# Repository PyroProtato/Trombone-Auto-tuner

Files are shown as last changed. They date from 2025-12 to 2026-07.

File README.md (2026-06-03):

# Trombone Autotuner



Hello! This is my first big personal hardware project. It's a custom autotuner for the Trombone! It should be able to detect whether the user is flat or sharp when playing a note and adjust the tuning slide to fit the pitch better.

I made this project because I want to get better at the hardware side of personal projects. I have been doing a lot of coding and game design in my free time, and I want to venture outside of my confort zone. I already know I have the skills necessary from my time in FRC robotics, so I want to make my own ideas come to life! This is one of those ideas that I had since I also enjoy playing the trombone and also I'm not the best at tuning :P

This is compatible specifically with the Yamaha Allegro Trombone with F Attachment



Wiring Diagram:


BOM (commercial products):
| Part | Amount | Price | Link |
| --- | --- | --- | --- |
| Linear Actuators | 2x | ~$48 | [https://www.digikey.com/en/products/detail/dfrobot/FIT0803/14824998](https://www.digikey.com/en/products/detail/dfrobot/FIT0803/14824998) |
| M3 Heatset Insert | 26x | $5.95 | [https://www.adafruit.com/product/4256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](https://www.adafruit.com/product/4256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) |
| M3 8mm bolts | 26x | $8.50 | [https://accu-components.com/us/metric-cap-head-screws/3818-SSCF-M3-8-A2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](https://accu-components.com/us/metric-cap-head-screws/3818-SSCF-M3-8-A2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) |
| M3 20mm bolts | 12x | $3.84 | [https://accu-components.com/us/metric-cap-head-screws/2802-SSC-M3-20-A2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](https://accu-components.com/us/metric-cap-head-screws/2802-SSC-M3-20-A2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) |
| M3 Hex Standoff | 8x | $3.57 | [https://ca.robotshop.com/products/m3-10mm-hex-standoff-mounting-kit-10pk](https://ca.robotshop.com/products/m3-10mm-hex-standoff-mounting-kit-10pk) |
| Arduino Uno | 1x | $30.88 | [https://everymarket.com/products/elegoo-uno-r3-control-board-usb-cable-for-arduino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](https://everymarket.com/products/elegoo-uno-r3-control-board-usb-cable-for-arduino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) |
| Duracell 9V Battery | 1x | $14.06 | [https://www.amazon.com/Duracell-Coppertop-Alkaline-Batteries-Count/dp/B000K2NW08?th=1](https://www.amazon.com/Duracell-Coppertop-Alkaline-Batteries-Count/dp/B000K2NW08?th=1) |
| L298N Motor Controller | 1x | $6.99 | [https://www.amazon.com/Qunqi-Controller-Module-Stepper-Arduino/dp/B014KMHSW6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](https://www.amazon.com/Qunqi-Controller-Module-Stepper-Arduino/dp/B014KMHSW6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) |
| Assorted Jumper Wires | ~10-12 | $6.98 | [https://www.amazon.com/Elegoo-EL-CP-004-Multicolored-Breadboard-arduino/dp/B01EV70C78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](https://www.amazon.com/Elegoo-EL-CP-004-Multicolored-Breadboard-arduino/dp/B01EV70C78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) |

BOM (3D Prints):
| Name | Amount |
| --- | --- |
| BottomHalf1 | 1x |
| BottomHalf2 | 1x |
| TopHalf1 | 1x |
| TopHalf2v2 | 1x |
| MotorMount | 2x |
| BottomMountTop | 2x |
| TopMotorMount | 2x |
| M3 Adapter | 2x |

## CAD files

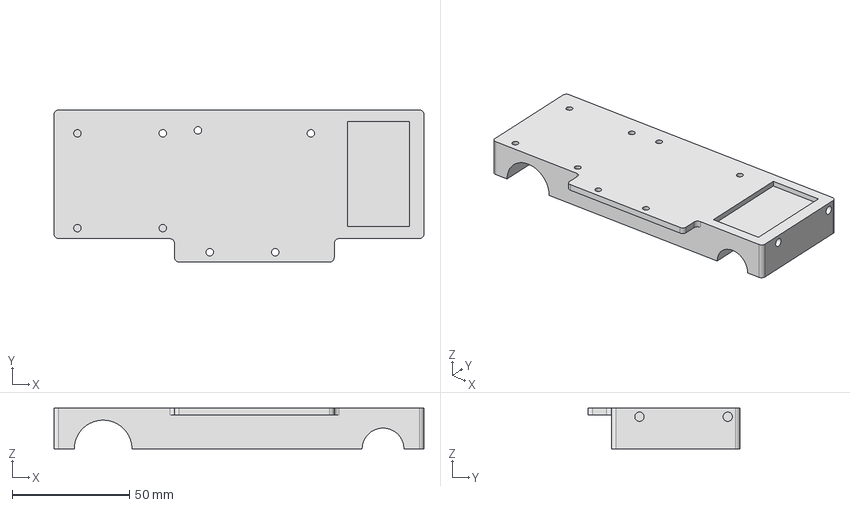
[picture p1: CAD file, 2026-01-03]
CAD/BottomHalf1.stp
158.1 x 65.0 x 17.5 mm

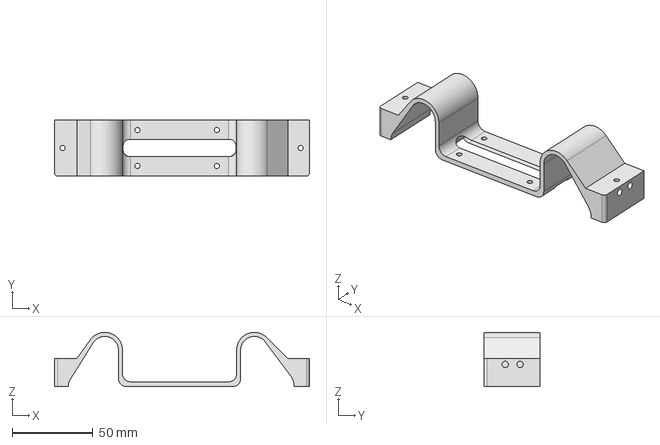
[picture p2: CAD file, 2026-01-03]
CAD/TopHalf2.stp
158.1 x 35.0 x 33.6 mm

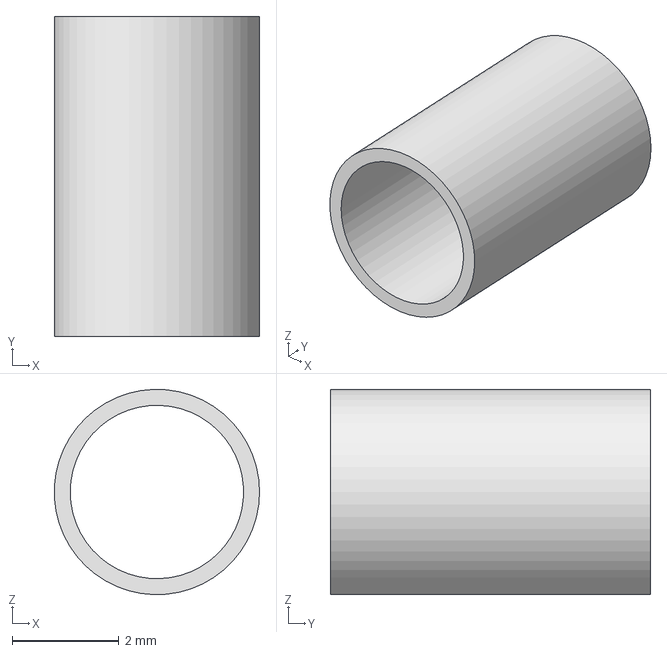
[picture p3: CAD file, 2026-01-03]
CAD/M3Adapter.stp
3.85 x 6.00 x 3.85 mm

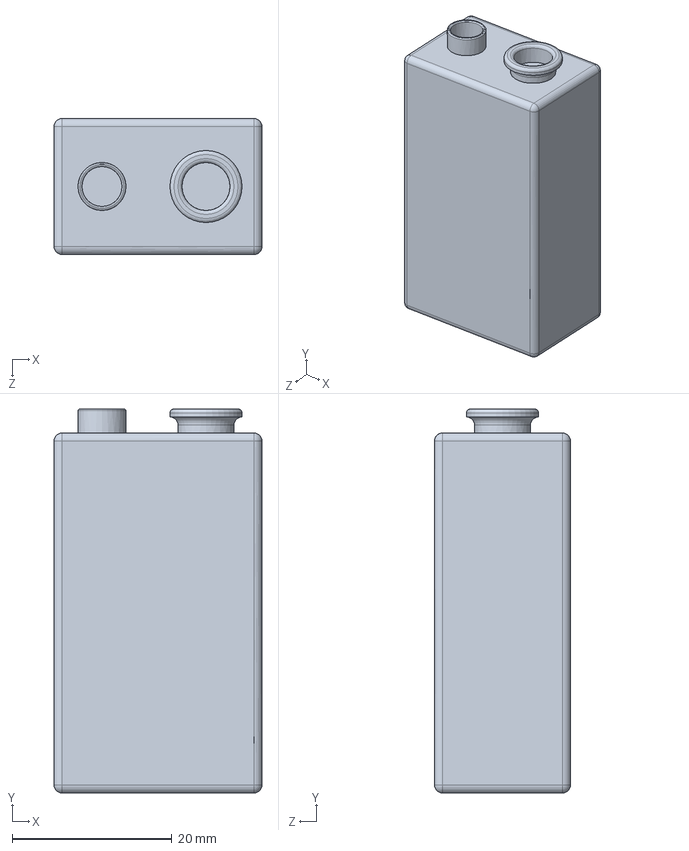
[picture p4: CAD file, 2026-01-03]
CAD/battery.SLDPRT
26.0 x 48.0 x 17.0 mm

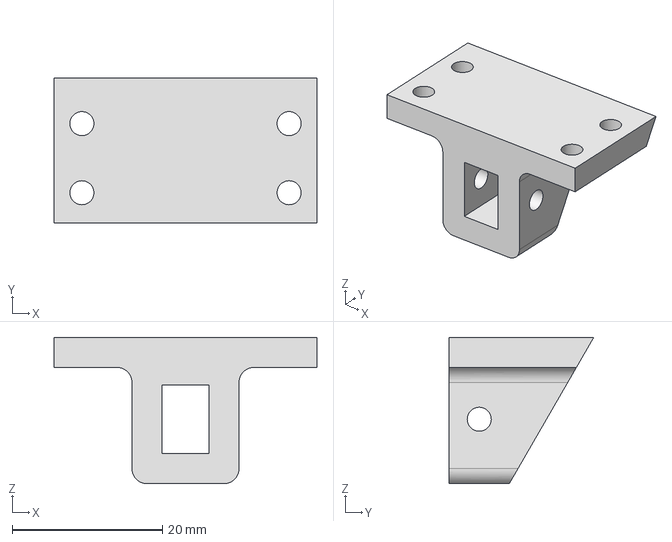
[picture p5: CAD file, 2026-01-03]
CAD/TopMotorMount.stp
35.0 x 19.2 x 19.5 mm

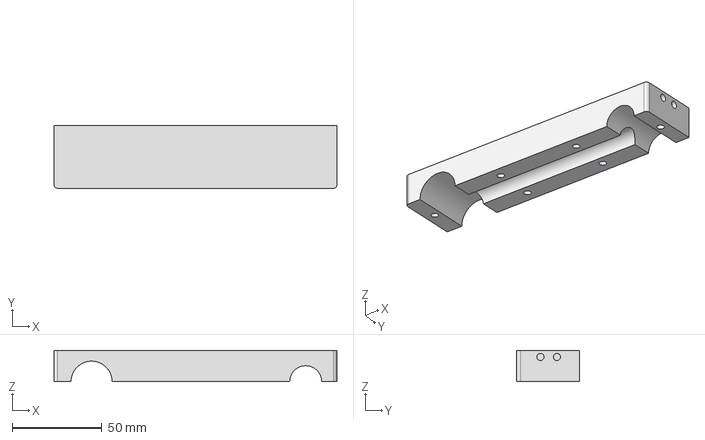
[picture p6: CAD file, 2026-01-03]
CAD/TopHalf1.stp
158.1 x 35.0 x 17.5 mm

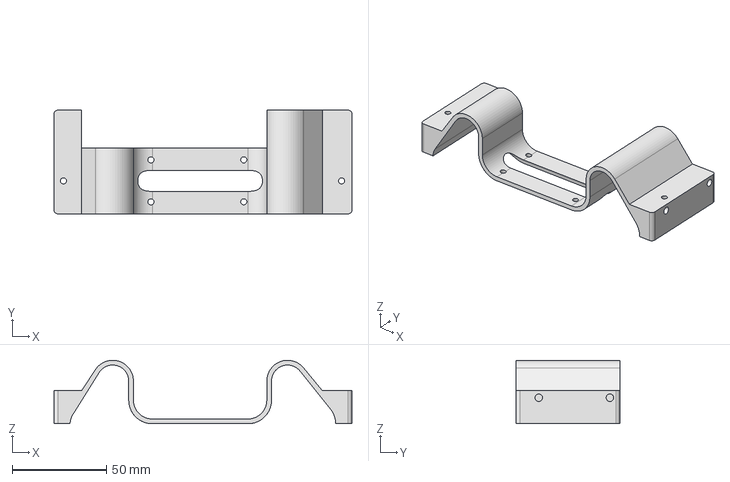
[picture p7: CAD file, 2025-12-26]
CAD/BottomHalf2.stp
158.1 x 55.0 x 33.6 mm

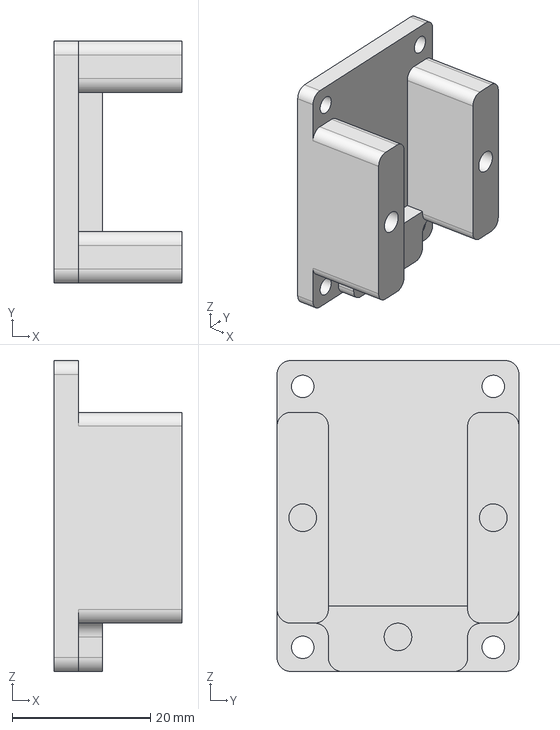
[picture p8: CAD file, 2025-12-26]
CAD/MotorMount.stp
18.5 x 35.0 x 45.0 mm

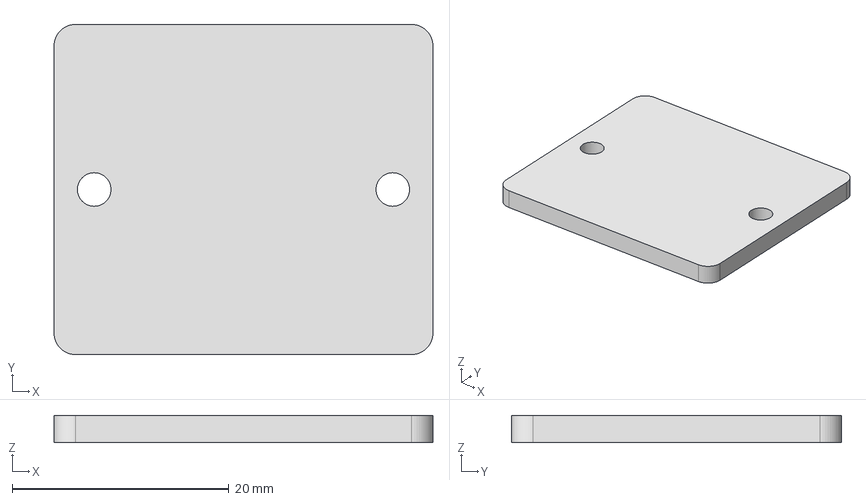
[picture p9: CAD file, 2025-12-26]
CAD/BottomMountTop.stp
35.0 x 30.5 x 2.50 mm

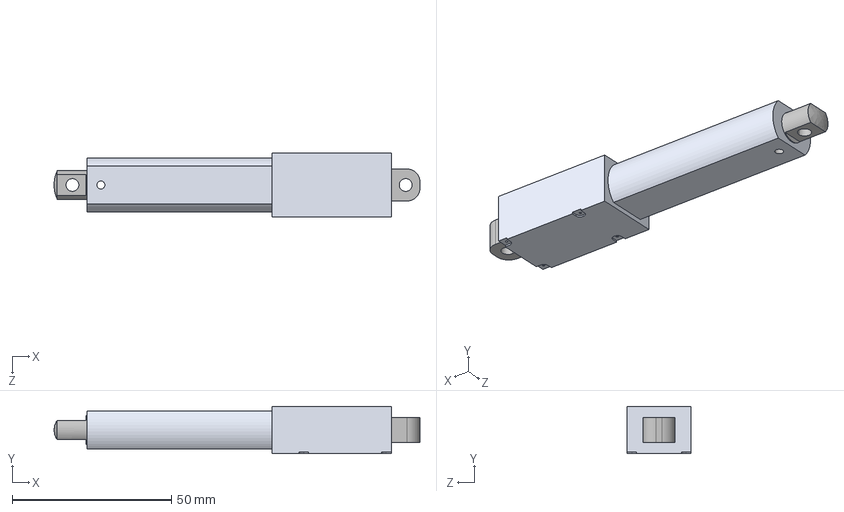
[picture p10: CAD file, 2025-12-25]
CAD/FIT0805.stp
114.8 x 14.8 x 20.0 mm

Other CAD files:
CAD/TopHalf2v2.stl
AutotunerCAD.iam
CAD/BottomBase.ipt
CAD/BottomHalf1.3mf
CAD/BottomHalf1.ipt
CAD/BottomHalf2.ipt
CAD/BottomMountTop.ipt
CAD/FIT0805.ipt
CAD/M3Adapter.ipt
CAD/MotorMount.3mf
CAD/MotorMount.ipt
CAD/TopBase.ipt
CAD/TopHalf1.ipt
CAD/TopHalf2.ipt
CAD/TopHalf2.stl
CAD/TopHalf2v2.ipt
CAD/TopMotorMount.3mf
CAD/TopMotorMount.ipt
CAD/battery.ipt
CAD/hexstandoff.ipt
OldVersions/AutotunerCAD.0011.iam
OldVersions/BottomBase.0014.ipt
OldVersions/BottomHalf1.0005.ipt
OldVersions/BottomHalf2.0005.ipt
OldVersions/ElectronicsHalf.0004.ipt
OldVersions/ElectronicsHalf.0005.ipt
OldVersions/ElectronicsHalf2.0001.ipt
OldVersions/ElectronicsHalf2.0002.ipt
OldVersions/M3Adapter.0001.ipt
OldVersions/MotorMount.0002.ipt
OldVersions/TopBase.0008.ipt
OldVersions/TopHalf1.0001.ipt
OldVersions/TopHalf2.0005.ipt
OldVersions/TopMotorMount.0004.ipt

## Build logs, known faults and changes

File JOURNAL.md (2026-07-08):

<!--
  This journal is auto generated by Stasis.
-->

# 1/5/2026 12 PM - Completed First Test

_Time spent: 2.2h_

Demo Video: [https://youtu.be/nVR0UZn7M2M](https://youtu.be/nVR0UZn7M2M)




This was my first test of the trombone autotuner. It didn't go that well tbh. After I attached everything including creating a makeshift mount for my 9V battery, it for some reason didn't work. I checked all of the electrical and eventually found out that it was an issue with one of the crimps I made. When I tried to take it out, the crimp fell off ;-;. Because of this, I had to get all my crimping stuff out and do 2 more crimps to replace the old one. After that, I still had to shuffle some things around, but it finally worked and fired both linear actuators at the same time. In the video above (or linked [here](https://youtu.be/nVR0UZn7M2M)) you can see my first test and how it actually moved the tuning slide.

Unfortunately, when I tried extending it further, it got caught on something and didn't go back down. I'm hoping the solution is just to put tuning slide oil on my tuning slide to make it not catch, but who knows. I have to bring my trombone to school tomorrow for band, so I took everything off, but when I next have time hopefully everything will be working!




# 1/2/2026 12 PM - Master Assembly and Preliminary Testing

_Time spent: 4h_





I did a lot of building work since the last devlog! I will start to list the things I had to do here:
 - Print all of the cadded parts (around 10-12 hours of printing)
 - Use my pinecil soldering iron to heatset ~32 M3 Inserts
 - Place and rewire the electrical components using standoffs
 - Solder the appropriate connections (see previous devlog)
 - Bolt everything in place (and strip a few bolt heads in the process oops...)
 - Disassemble and Reassemble multiple times since this took a few days and I needed to practice trombone like regular without a bunch of cables stabbing me in the neck
 - Adjust things like cable management
 - Troubleshoot issues with motor power (see below)

The thing that ended up taking the most time was with a motor power issue. Both of the linear actuators I am using are recommended for 9V of electricity. When I was testing just the code by itself in the first few devlogs, I was able to use a 5V supply to power one just fine. However, now I realized that when 2 were connected there was not enough voltage to move both, and as such neither moved. This ended up taking a decent amount of time first to diagnose the problem (I thought it was a code issue or an electrical issue because I'm not that familiar with the l298N module) and then to figure out a solution. I ended up taking a 9V battery (that I luckily already made space for in the print) and e-taping wires to both poles to run its 9V into the motor controller. Now it works much better and more powerful.

With all of this settled, the last thing to do is to get all of the finishing touches done and finally test the completed product. Fingers crossed that not _too_ much will need to be changed...





# 12/29/2025 11 PM - Learned how to Crimp Wires

_Time spent: 3.5h_



So, it took me so long to learn how to crimp wires. In my robotics team, I'm more on the mechanical and design side, so I haven't actually learned how to crimp wires yet. I had my dad teach me but he's a little rusty himself, so it took a while for us to actually figure out how to do it. After I figured out the concept behind it though, it took us a while to actually manuever the crimp with the wire into the crimper, but we found out that the crimper we have is actually way too big for the wires that I have to use. So, I ended up basically just using needle nose pliers for this which is way more tedious and way more time consuming. Just to make the first two all in all it took me around 2.5 hours. Its cooked lol.



# 12/29/2025 4 PM - Finished CAD for electronics mount

_Time spent: 2.3h_




I finished adding a dedicated mounting place for all of the electronics necessary (including the arduino, l298N motor driver, and 9V duracell battery). For the arduino, I looked at online dimensions to get the mounting holes in the perfect location, but for the l298N and the battery I had to measure them myself using the dial caliper. I tried to design it so that it wouldn't hit your head while playing the trombone, but even though I tried it still might. Also, I ended up using hex standoffs to space each electrical component away from the base a bit so that it can attach well (since there are solder blobs on the backsides of them. With this, I should be able to print everything and assemble them all together, and hopefully it will work! Wish me luck!




# 12/27/2025 12 PM - Finished CAD for the top mount

_Time spent: 2.8h_

Draft 1: 

Draft 2: 

I finished the CAD for the top motor mount! This one was a bit easier since I could sorta use the designs I made for the bottom as a template. However, once again I forgot that I needed to add extra space for another valve so I had to remake that part again -_- Additionally, I had to make a different connector for the motor to the mount which actually turned out to be kinda difficult since I want it to be strong and to fit perfectly for the motor so it doesn't shake around. I printed adapters for the M3 bolts I have to make their diameter a bit bigger (~4mm) to fit better in the linear actuator's mounting hole. After this, I think that it will work a lot better! Next step is cadding the part for the electronics.




# 12/26/2025 12 PM - Finished CAD for the bottom Mount

_Time spent: 3.7h_

Draft 1: 
Draft 2: 

Printed Prototypes:



This was the next step in the CAD for the trombone mount. I finished the full bottom mount part by taking precise measurements with my dial caliper. I had to redesign the bottom part a few times since in my first draft, I forgot that their was another tube in the way, so I had to redesign it to accomodate said tube. I printed it and it fits pretty well! Additionally, I also designed and printed motor mounts. They also required 2 different tries, and they are designed to be easily hotswappable and to keep the motor steady with only 1 mounting hole (see pictures above). Next step is to cad the top part of the mount!







# 12/25/2025 12 PM - Started CAD for the bottom part of the mount.

_Time spent: 2.5h_




This is the beginning of the CAD for the autotuner mount which will ultimately be 3D printed. This should grab the bottom part of my trombone's tuning slide (see pictures above). I'm planning on splitting this print into 4 main parts, 2 on the bottom and 2 on the top. The bottom and top are split into 2 in order to allow for easy mounting, and the linear actuators which are mounted to the bottom should extend to push the top part. Hopefully, you will see more of the idea in the upcoming journal entries!




# 11/28/2025 12 PM - Wrote script to detect Trombone Pitches

_Time spent: 4.8h_



Alright, this one also took a while for a variety of reasons. I wanted to write a script in python to detect trombone pitches. 

I tried to install pyaudio to help with this, but that didn't work, so I installed other packages. First I tried FFT, but apparently it doesn't work well for instruments since they have harmonics and whatnot, so I switched to Aubio. Now the pitches were somewhat accurate, but they weren't the best. 
I spent a while trying to write a script to filter out outliers in the readings and detect when there is a note change, which is actually kinda hard, before I realized that I was overcomplicating things. I then came up with a much simpler system that works relatively similar. 

Then after fiddling with the audio on my computer for a bit for the best capture, I hooked it up to the linear actuator for it to move accordingly, and for the most part it worked! Next step is to CAD the mechanical parts of it (like the mounts for the electronics and the linear actuators) so that they can be 3D-printed!





# 11/26/2025 12 PM - Figured out how to control the linear actuator with code!

_Time spent: 1h_

[Demo Video](/user-attachments/blobs/proxy/eyJfcmFpbHMiOnsiZGF0YSI6MTQ5NjYsInB1ciI6ImJsb2JfaWQifX0=--15b4b04ea5803bb51493dcab344ed8e98d156e8b/IMG_3155.mp4)



Figured out how to control the linear actuator with code using the Pyserial module in combination with modifying the arduino sketch! Now, I just have to figure out how to connect an external tuner either on my computer or a real life one to control the software, this controlling the linear actuator. Wish me luck!




# 11/23/2025 12 PM - Finished Preliminary Research + Testing

_Time spent: 5.2h_

[Demo Video](/user-attachments/blobs/proxy/eyJfcmFpbHMiOnsiZGF0YSI6MTM4MzUsInB1ciI6ImJsb2JfaWQifX0=--bdc5eb02dfd11cb8d1dd613ace2ad7bc0eb4a4ee/IMG_3154.mp4)





Hey! This journal was mostly a ton of research, purchasing, testing and other things. 

First of all, I had to research ways to make this project possible I knew I wanted to use linear motion in some way to push the tuning slide but that was about it. Using research and a digikey credit card I got from SoM, I found the DFRobot linear actuators were cheap and perfect for this task. I also found that I need a motor controller which I slavaged from an arduino-based car my brother made along with an arduino and some other miscellaneous components.

After my linear actuators came in, I started experimenting with them. It took an embarassingly long time to figure out how to operate the motor controller since it wasn't the standard l298n motor controller. In particular, I had to find out how to wire a 6v power supply separately to the motor controller, which I ended up doing using the battery holders from my snap circuits box (lol). Also, since the linear actuators didn't fit perfectly into the motor board, I had to strip some wires and I will add some solder later as well to stiffen them in order to adapt it over.

Finally, I had to write the software for it. This was significantly easier since it was pretty simple (just set pins to high and low to change direction) but I did still run into a few issues with syntax and compiliing since I have never used C++ before.

Overall, although the end product isn't too impressive, it took a lot of effort and learning since I'm new to this lol.




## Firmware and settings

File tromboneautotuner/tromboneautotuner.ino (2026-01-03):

// Define the pins connected to the OSOYOO module
#define IN1 6   // Motor A direction pin 1
#define IN2 7   // Motor A direction pin 2
#define ENA 5   // Motor A enable pin (PWM speed control)

#define IN1B 11   // Motor B direction pin 1
#define IN2B 12   // Motor B direction pin 2
#define ENAB 10   // Motor B enable pin (PWM speed control)

void setup() {
  // Set the control pins as outputs
  pinMode(IN1, OUTPUT);
  pinMode(IN2, OUTPUT);
  pinMode(ENA, OUTPUT);

  pinMode(IN1B, OUTPUT);
  pinMode(IN2B, OUTPUT);
  pinMode(ENAB, OUTPUT);

  // Initialize motor to stop
  stopMotor();

  Serial.begin(9600);
}

void loop() {
  if (Serial.available() > 0) {
    String receivedData = Serial.readStringUntil('\n'); // Read until newline character
    if (receivedData == "in") {
      rotateClockwise(255);
    } else if (receivedData == "out") {
      rotateCounterClockwise(255);
    } else if (receivedData == "stop") {
      stopMotor();
    }
  }

  
}

// Function to rotate the motor clockwise with speed control (0-255)
void rotateClockwise(int speed) {
  digitalWrite(IN1, HIGH);  // Set IN1 High
  digitalWrite(IN2, LOW);   // Set IN2 Low
  analogWrite(ENA, speed);  // Enable motor with specified speed
  digitalWrite(IN1B, HIGH);  // Set IN1 High
  digitalWrite(IN2B, LOW);   // Set IN2 Low
  analogWrite(ENAB, speed);  // Enable motor with specified speed
}

// Function to rotate the motor counter-clockwise with speed control (0-255)
void rotateCounterClockwise(int speed) {
  digitalWrite(IN1, LOW);   // Set IN1 Low
  digitalWrite(IN2, HIGH);  // Set IN2 High
  analogWrite(ENA, speed);  // Enable motor with specified speed
  digitalWrite(IN1B, LOW);   // Set IN1 Low
  digitalWrite(IN2B, HIGH);  // Set IN2 High
  analogWrite(ENAB, speed);  // Enable motor with specified speed
}

// Function to stop the motor (free stop state)
void stopMotor() {
  // Alternatively, setting both IN1/IN2 to HIGH or LOW results in a brake state
  analogWrite(ENA, 0); // ENA signal 0 puts motor in free stop state
  analogWrite(ENAB, 0); // ENA signal 0 puts motor in free stop state
}

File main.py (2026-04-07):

import serial
import time

import sys
import aubio
from scipy.fftpack import fft, fftfreq


import sounddevice as sd
import numpy as np
import aubio
import math
import sys

# --- Configuration ---
FS = 44100         # Sample rate in Hz
CHANNELS = 2       # Mono input
BLOCKSIZE = 1024   
HOP_SIZE = 512     

average = 0
total = 0
bigsamples = []
SAMPLES_SIZE = 10

smallavg = 0
smalltotal = 0
smallsamples = []
SMALL_SAMPLES_SIZE = 3


#Pitches
PITCH_FREQUENCIES = {
    'A0': 27.50,
    'A#0': 29.14,
    'B0': 30.87,
    'C1': 32.70,
    'C#1': 34.65,
    'D1': 36.71,
    'D#1': 38.89,
    'E1': 41.20,
    'F1': 43.65,
    'F#1': 46.25,
    'G1': 49.00,
    'G#1': 51.91,
    'A1': 55.00,
    'A#1': 58.27,
    'B1': 61.74,
    'C2': 65.41,
    'C#2': 69.30,
    'D2': 73.42,
    'D#2': 77.78,
    'E2': 82.41,
    'F2': 87.31,
    'F#2': 92.50,
    'G2': 98.00,
    'G#2': 103.83,
    'A2': 110.00,
    'A#2': 116.54,
    'B2': 123.47,
    'C3': 130.81,
    'C#3': 138.59,
    'D3': 146.83,
    'D#3': 155.56,
    'E3': 164.81,
    'F3': 174.61,
    'F#3': 185.00,
    'G3': 196.00,
    'G#3': 207.65,
    'A3': 220.00,
    'A#3': 233.08,
    'B3': 246.94,
    'C4': 261.63,  # Middle C
    'C#4': 277.18,
    'D4': 293.66,
    'D#4': 311.13,
    'E4': 329.63,
    'F4': 349.23,
    'F#4': 369.99,
    'G4': 392.00,
    'G#4': 415.30,
    'A4': 440.00,  # Concert Pitch Standard
    'A#4': 466.16,
    'B4': 493.88,
    'C5': 523.25,
    'C#5': 554.37,
    'D5': 587.33,
    'D#5': 622.25,
    'E5': 659.25,
    'F5': 698.46,
    'F#5': 739.99,
    'G5': 783.99,
    'G#5': 830.61,
    'A5': 880.00,
    'A#5': 932.33,
    'B5': 987.77,
    'C6': 1046.50,
    'C#6': 1108.73,
    'D6': 1174.66,
    'D#6': 1244.51,
    'E6': 1318.51,
    'F6': 1396.91,
    'F#6': 1479.98,
    'G6': 1567.98,
    'G#6': 1661.22,
    'A6': 1760.00,
    'A#6': 1864.66,
    'B6': 1975.53,
    'C7': 2093.00,
    'C#7': 2217.46,
    'D7': 2349.32,
    'D#7': 2489.02,
    'E7': 2637.02,
    'F7': 2793.83,
    'F#7': 2959.96,
    'G7': 3135.96,
    'G#7': 3322.44,
    'A7': 3520.00,
    'A#7': 3729.31,
    'B7': 3951.07,
    'C8': 4186.01
}



# --- Initialize aubio Pitch Detection with YIN algorithm ---
# YIN is generally more accurate for musical instruments with rich harmonics.
p = aubio.pitch("yin", BLOCKSIZE, HOP_SIZE, FS) 

# Set parameters for a more stable tuner experience:

# Use 'midi' unit for better understanding of note boundaries, we convert back to Hz for display
p.set_unit("Hz") 

# Tolerance: Lower tolerance makes it more strict (can drop out if noisy)
# Higher tolerance is more 'forgiving' but might jump notes. 0.8 is a good balance.
p.set_tolerance(0.75) 

# Silence Threshold: Below this dB value, no pitch is detected
p.set_silence(-45) # Set a lower threshold for brass instruments to prevent noise


def aubio_audio_callback(indata, frames, time, status):
    global average
    global total
    global bigsamples

    global smallavg
    global smalltotal
    global smallsamples
    
    assert frames == HOP_SIZE, f"Callback frames size mismatch: expected {HOP_SIZE}, got {frames}"
    
    if status:
        print(status, file=sys.stderr)
    
    samples = indata[:, 0].astype(aubio.float_type)

    pitch_hz = p(samples)[0] # Get the frequency value
    confidence = p.get_confidence() # Get the confidence value (float)

    #Volume
    volume_norm = np.sqrt(np.mean(samples**2)) * 1000 
    db_level = 20 * np.log10(volume_norm + 1e-10)


    #Detects if each pitch should be heard
    if pitch_hz > 0 and confidence > 0.3 and db_level > 55.0: # aubio returns 0 Hz if it detects silence/no confident pitch
        #print(f"Detected Frequency: {abs(pitch_hz):.2f} Hz (Confidence: {confidence:.2f}) Volume: {db_level}")

        total += pitch_hz
        bigsamples.append(pitch_hz)
        
        
        if len(bigsamples) > SAMPLES_SIZE:
            total -= bigsamples[0]
            del bigsamples[0]
    
        average = total/len(bigsamples)

        target = PITCH_FREQUENCIES[pitch(average)]
        action = ""
        if average < target:
            action = "flat"
            ser.write(b'in\n')
        else:
            action = "sharp"
            ser.write(b'out\n')

        print(f"{pitch(average)} {action} {average-target}")

    else: 
        
        ser.write(b"stop\n")




       


def eliminate_outliers_percentile(data_list, lower_p=5, upper_p=95):
    """
    Eliminates data points outside the specified percentile range.
    """
    data_arr = np.array(data_list)
    # Calculate the 5th and 95th percentiles
    lower_bound = np.percentile(data_arr, lower_p)
    upper_bound = np.percentile(data_arr, upper_p)
    
    # Filter the data to keep only values within the bounds
    cleaned_list = data_arr[(data_arr >= lower_bound) & (data_arr <= upper_bound)].tolist()
    return cleaned_list



def pitch(freq):
    # A4 (440 Hz) is 4.75 octaves above C0 in a 16 Hz based system
    A4 = 440
    C0 = A4 * math.pow(2, -4.75) 
    
    # Note names in an octave
    name = ["C", "C#", "D", "D#", "E", "F", "F#", "G", "G#", "A", "A#", "B"]
    
    # Calculate the number of half steps 'h' from C0
    # The formula h = 12 * log2(P / C0) is used
    h = round(12 * math.log2(freq / C0))
    
    # Calculate the octave and the note name index
    octave = h // 12
    n = h % 12
    
    # Return the note name and octave as a combined string
    return name[n] + str(octave)




try:
    ser = serial.Serial(
        port='COM6',        # Replace with your port
        baudrate=9600,
        bytesize=8,
        parity='N',
        stopbits=1,
        timeout=1
    )
    print(f"Connected to {ser.name}") 
    time.sleep(2)
    

except serial.SerialException as e:
    print(f"Error: {e}")



time.sleep(2)

ser.write(b'out\n')

time.sleep(2)

ser.write(b"in\n")

time.sleep(3)

ser.write(b"stop\n")

"""
print("Starting Aubio YIN pitch stream... Press Ctrl+C to stop.")
try:
    with sd.InputStream(samplerate=FS, blocksize=HOP_SIZE, channels=CHANNELS, callback=aubio_audio_callback):
        while True:
            sd.sleep(1000) 
except KeyboardInterrupt:
    print("\nStream stopped by user.")
except Exception as e:
    print(f"An error occurred: {e}")

"""

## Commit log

2025-12-26 Bottom Mount CAD
    [AutotunerCAD.0001.iam, AutotunerCAD.0004.iam, AutotunerCAD.iam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]
2026-04-07 File organization
    [BottomBase.ipt, BottomHalf1.3mf, BottomHalf1.ipt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]
2026-06-03 Wiring Diagrams
    [Wiring.kicad_pcb, Wiring.kicad_sch]
2026-06-16 Added BOM csv
    [BOM.csv]
